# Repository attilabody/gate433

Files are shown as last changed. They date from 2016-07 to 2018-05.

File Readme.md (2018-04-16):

# Shared parking space access controller

## Features

Gate433 uses cheap, standard (and insecure) gate opener remotes operating on 433 MHz to control entry and exit of vehicles allowed to acces the parking area.

Each gate opener supposed to be assigned to one vehicle and has unique code. The main purpose of it is to make unfair usage of the parking as inconvinient as possible using commodity gate opener remotes.

Features list:

* 1024 possible remote codes
* Position of each vehicle (inside, outside, unknown) is remembered. Gate opening will be denied for unexpected movements (e.g vehicle which is already inside tries to enter again)
* Access time limits by direction can be set independently for any vehicle (e.g can enter Monday to Friday from 08:30 to 17:00, can leave Monday to Friday from 08:30 to 17:30)
* Vehicle database snd device configuration stored in EEPROM
* Log stored on SD card
* Database changes can be imported from SD card
* Exceptional days (e.g. National holydays) database on SD card
* Automatic DST handling
* Simple command line interpreter on serial for database manipulation, date/time setting, log manipulation and temperature query

## Hardware

There are two versions of the hardware: Original version used Arduino Nano as central component. It is obsoleted by the newer version based on a popular STM32F103C8T6 based minimal board widely known as BluePill. It's actually cheaper on eBay or Aliexpress than the total cost of the components it contains.

Both versions ar using two inputs (usually coming from inductive loop detectors) in addition to the RF signal to decide if a vehicke intends to enter or exit. A pair of tricolor traffic lights provide feedback for drivers.

Both versions have 6 opto-isolated open drain output for 12V LED traffic lights,one opto-isolated open collector output for gate opening and two opto-isolated input for inductive loop detectors.

Second iteration have three extra features compared to the first:

* WiFi to serial bridge for wireless communication
* Rotary encoder driven simpe user interface (yet to be implemented in the firmware)
* 3D printable case modelled in FreeCAD

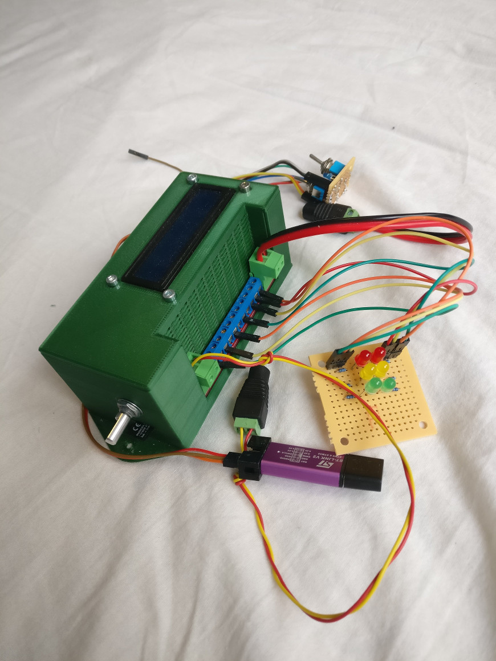
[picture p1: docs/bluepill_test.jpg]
V2


Prototype of STM32 based version

## Firmware

Arduino Nano based firware was built on Arduino framework using Sloeber Arduino IDE. Source files persist in folders named "gatekeeper", "common" and "libs".  
STM32 version is completely separated as it is based on STM32Cube framework. STM32 sources are placed in "gatekeeper-stm32" and "stm32goodies" folder.

## Schematics and PCB

Arduino based first version hardware developed using proprietrary Eagle free version, and obsoleted by STM32 version but schematics of the [mainboard](docs/V1_mainboard.pdf) and the [IO panel](docs/V1_extio.pdf) are still available for reference.

As mentioned above, hardware of STM32 version designed using KiCAD. The complete EDA project is available in the hardware/STM32 folder. Here are the [schematics](docs/bluepill.pdf) in PDF for easier access.

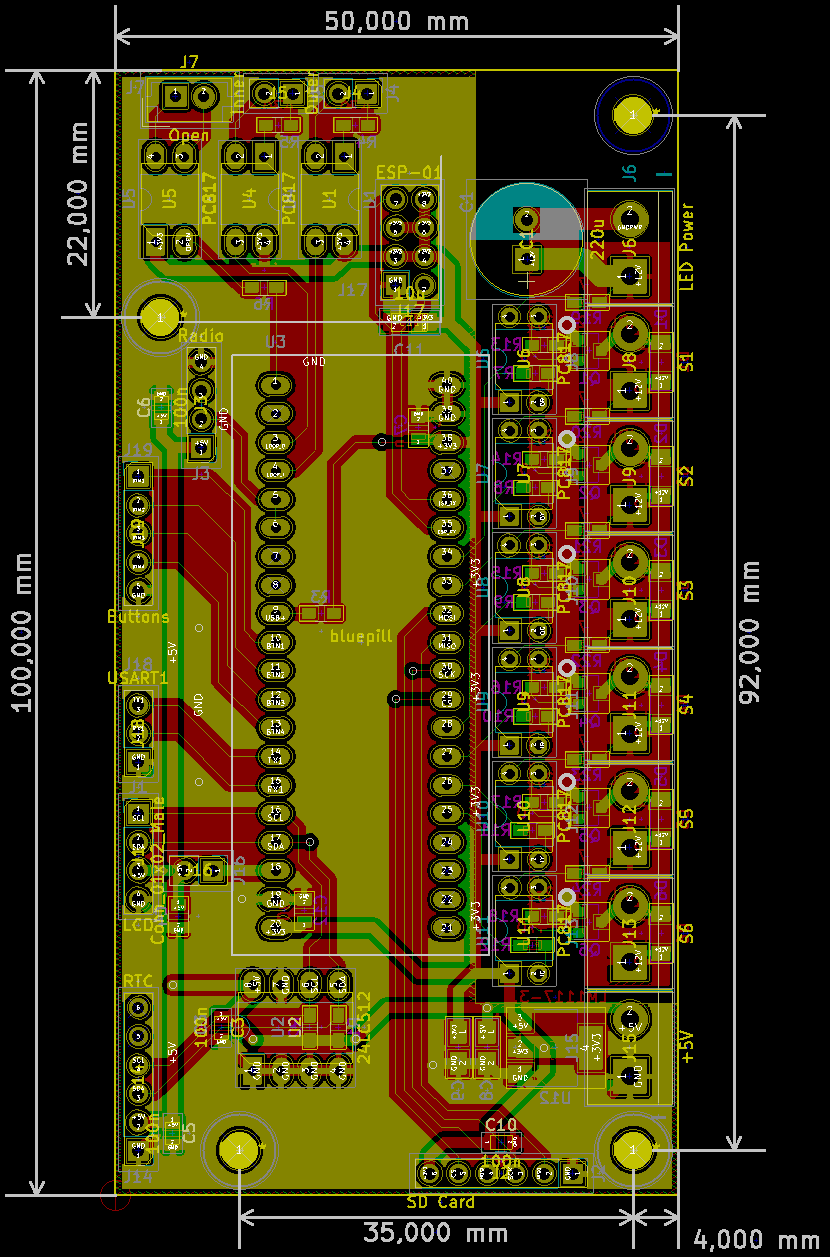
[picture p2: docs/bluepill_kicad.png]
bluepill_kicad


PCB design for STM32 bsed version

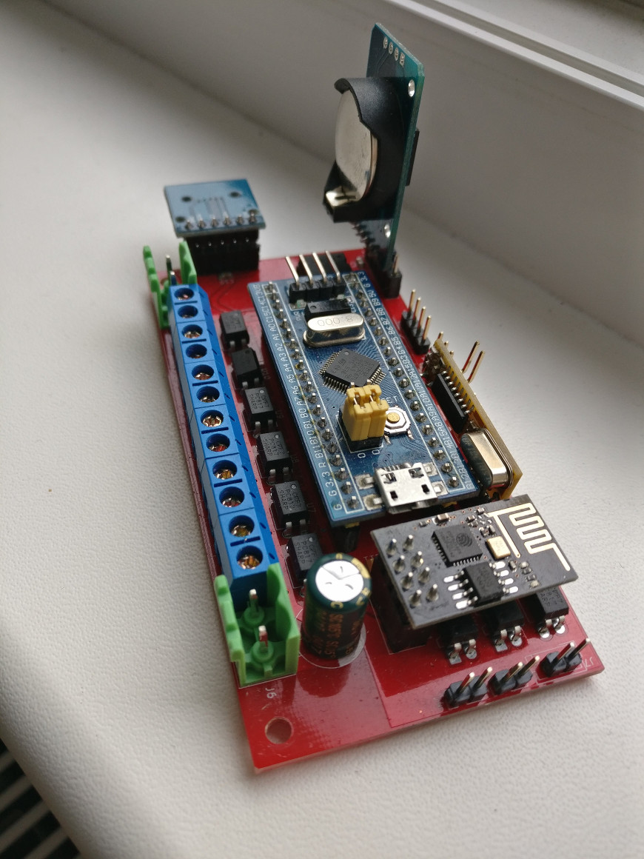
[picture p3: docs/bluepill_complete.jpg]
bluepill_complete


Assembled STM32 panel with modules installed

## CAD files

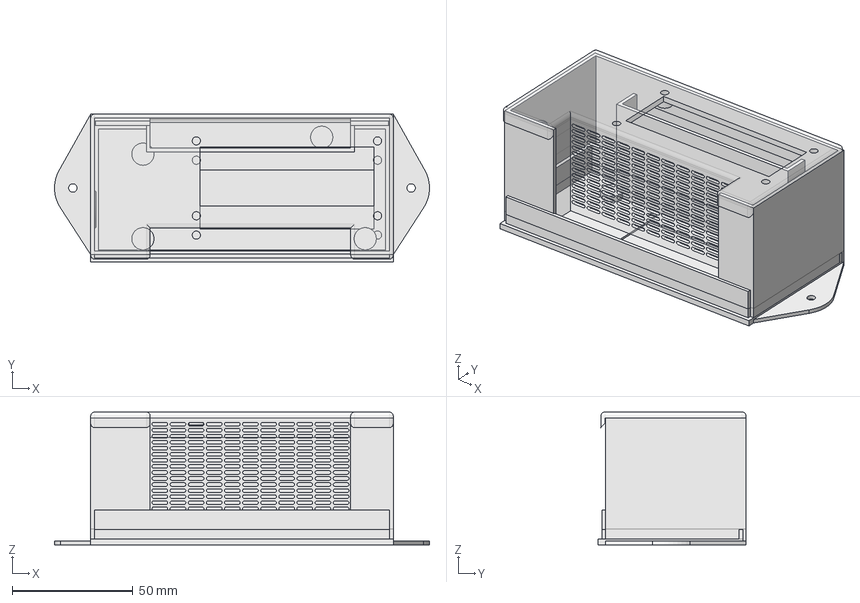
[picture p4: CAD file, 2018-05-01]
hardware/stm32/GateKeeperCase.fcstd
155.2 x 61.2 x 55.0 mm
EncoderHemChamf
Clone of Cap
Bottom
walls_low
walls_high
sdhole

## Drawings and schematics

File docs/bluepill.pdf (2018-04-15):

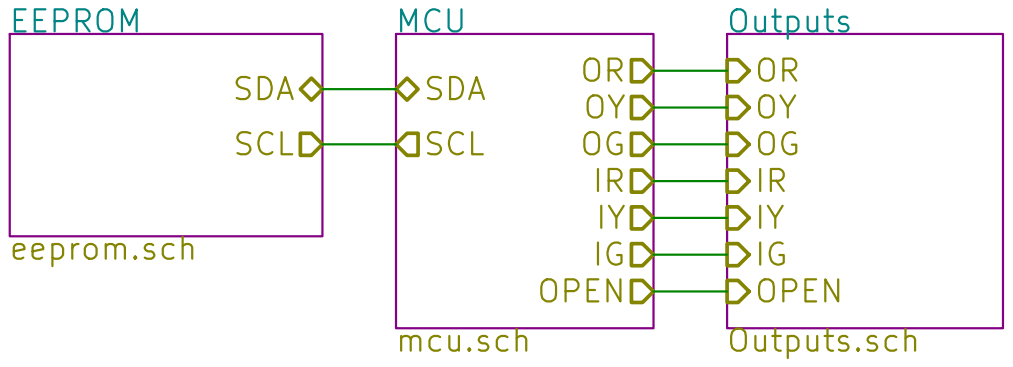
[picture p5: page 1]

File: bluepill.sch Sheet: / EEPROM

MCU mcu.sch SDA

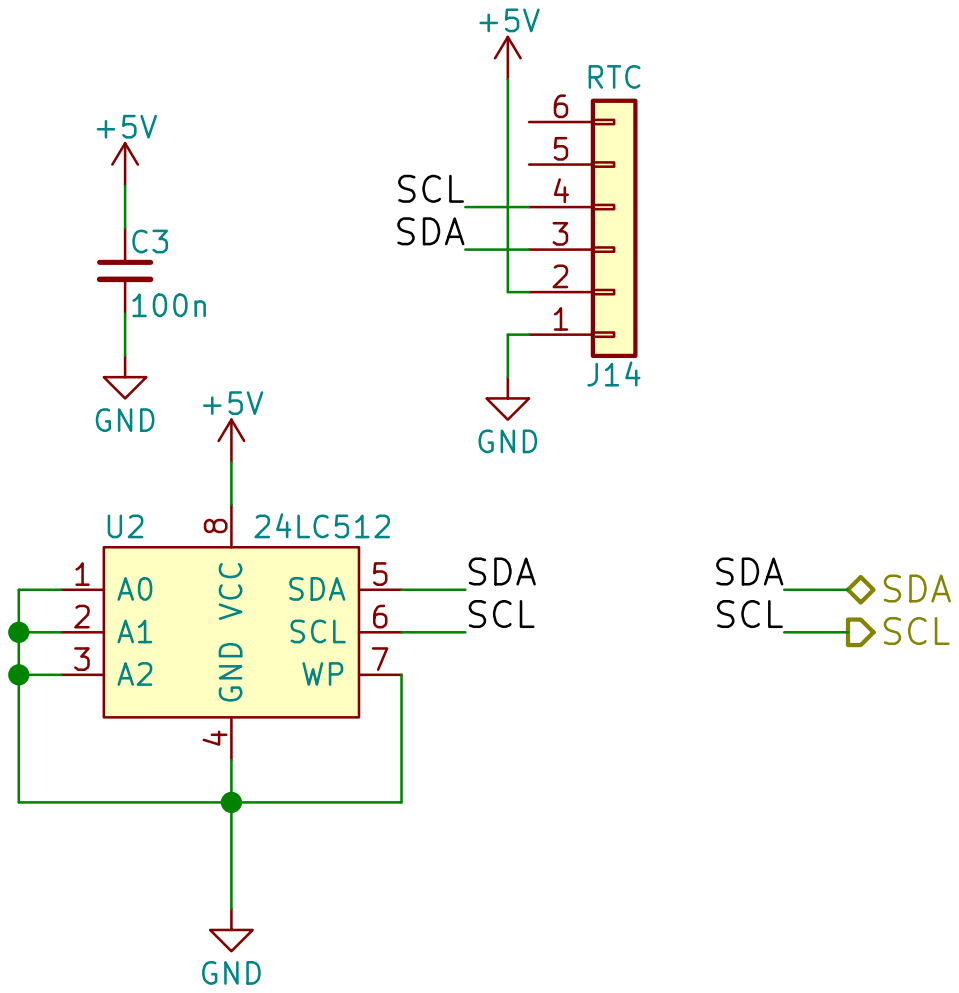
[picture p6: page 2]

8 A0 1 A1 2 A2 3 SDA 5 SCL 6 WP 7 U2 24LC512 SCL

File: eeprom.sch Sheet: /EEPROM/ GND

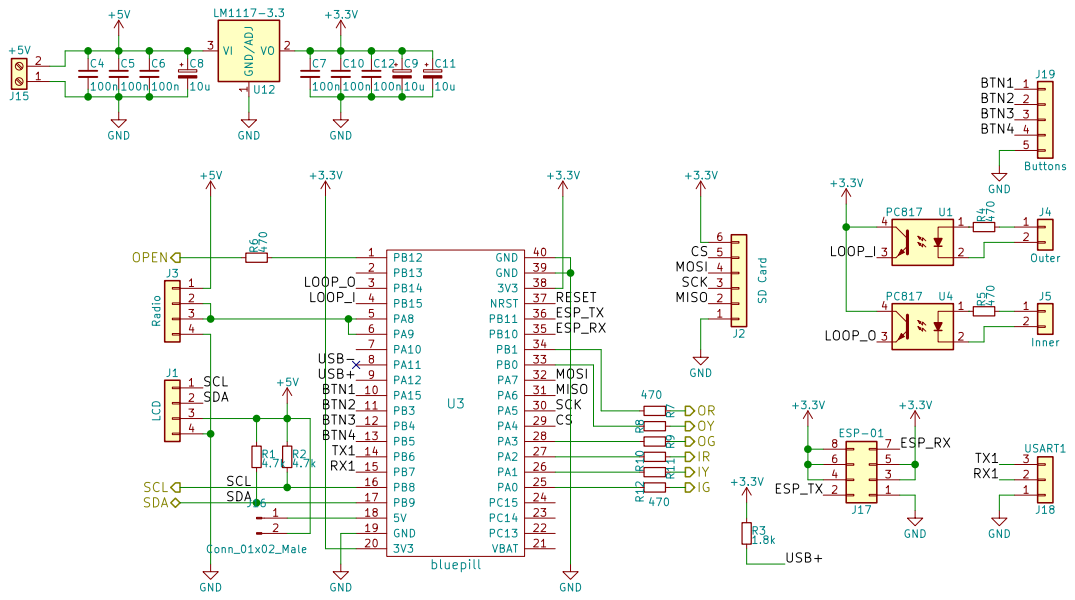
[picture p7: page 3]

SDA

Id: 3/4 Title: File: mcu.sch Sheet: /MCU/

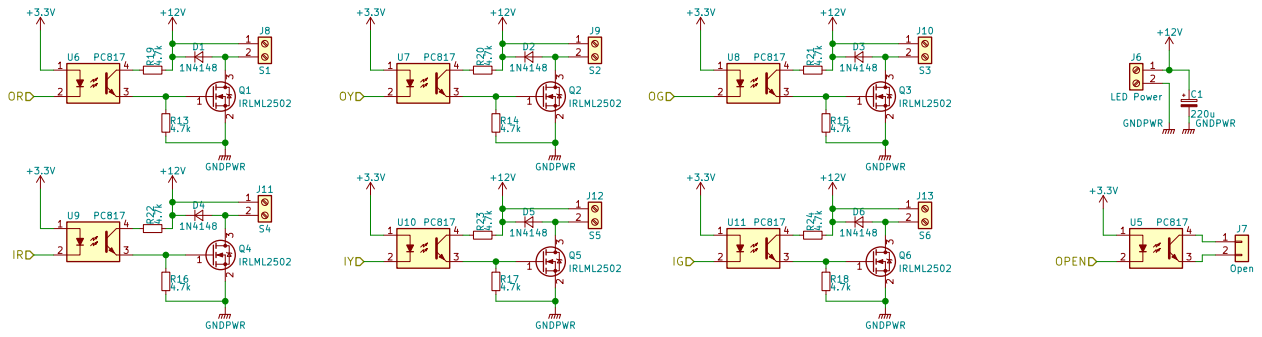
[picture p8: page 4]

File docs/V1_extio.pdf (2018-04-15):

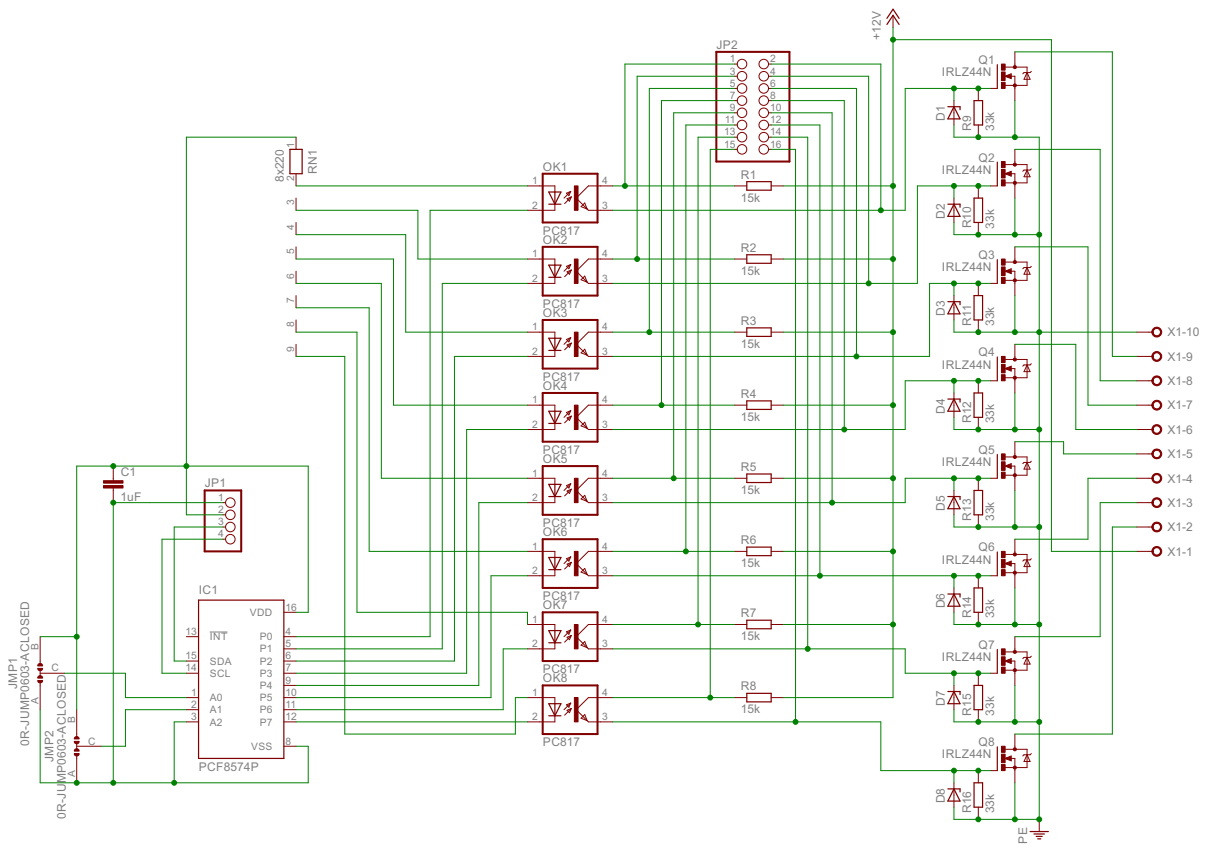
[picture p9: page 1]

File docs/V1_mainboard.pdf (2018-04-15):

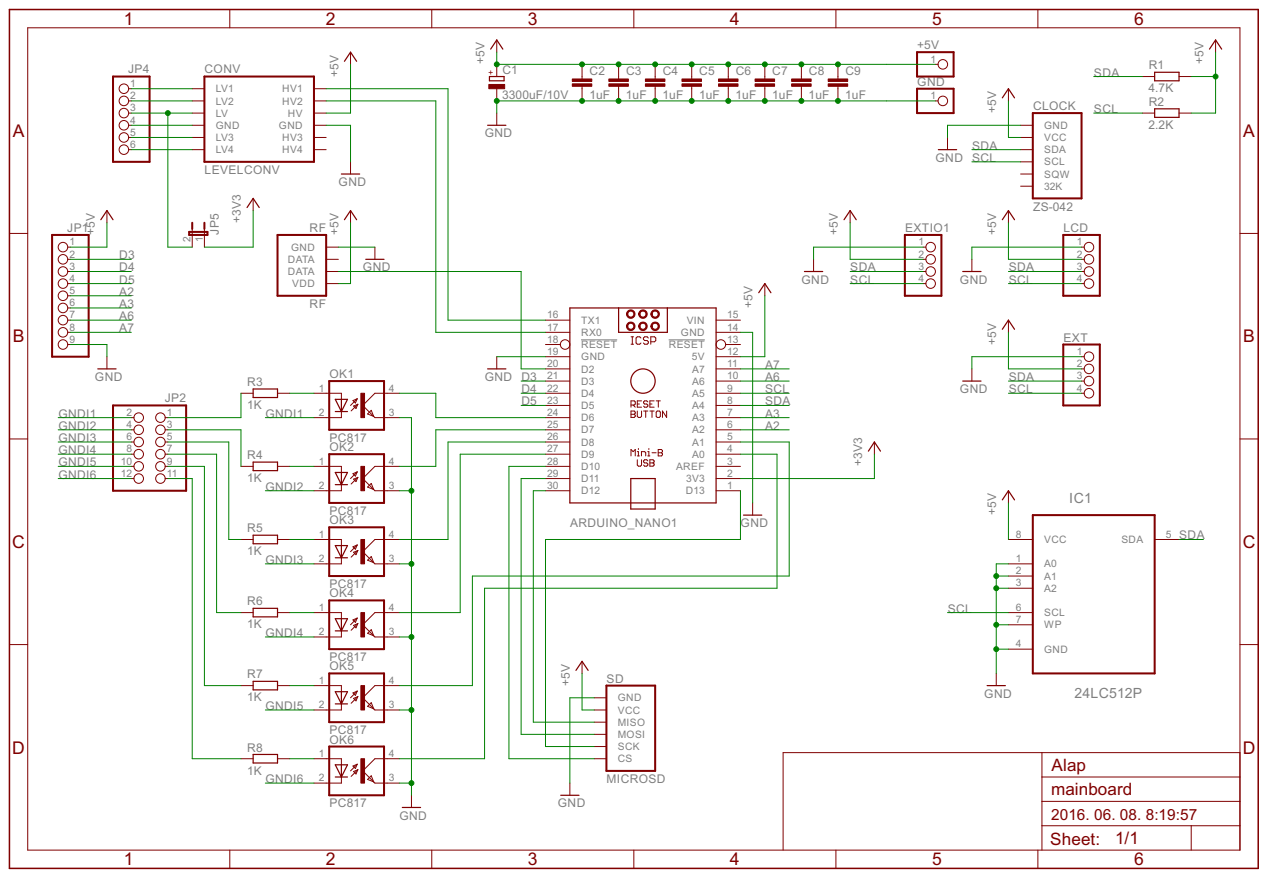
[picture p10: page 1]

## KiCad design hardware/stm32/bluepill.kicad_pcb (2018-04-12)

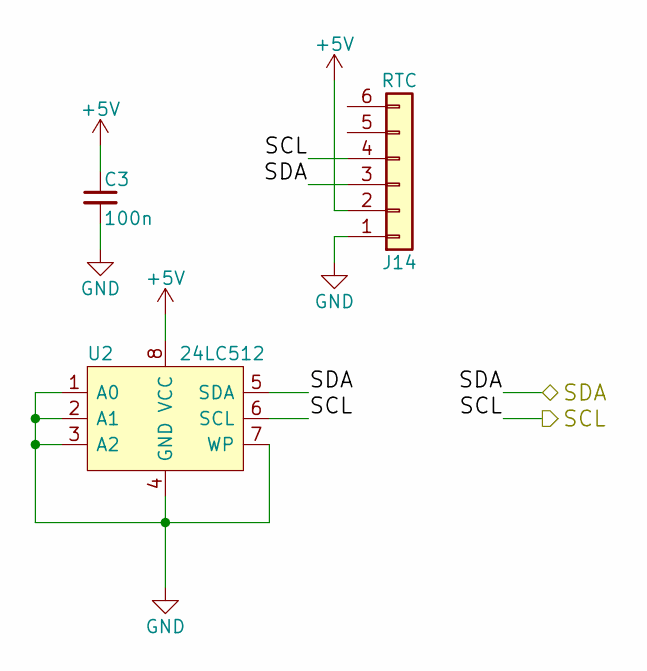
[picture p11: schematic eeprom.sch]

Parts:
C3: 100n; C_0805
J14: RTC; Pin_Header_Straight_1x06_Pitch2.54mm
U2: 24LC512; DIP-8_W7.62mm_LongPads

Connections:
+5V: C3.1, J14.2, U2.8 (VCC); also elsewhere on the board
/EEPROM/SCL: J14.4, U2.6 (SCL); also elsewhere on the board
/EEPROM/SDA: J14.3, U2.5 (SDA); also elsewhere on the board
GND: C3.2, J14.1, U2.1 (A0), U2.2 (A1), U2.3 (A2), U2.4 (GND), U2.7 (WP); also elsewhere on the board

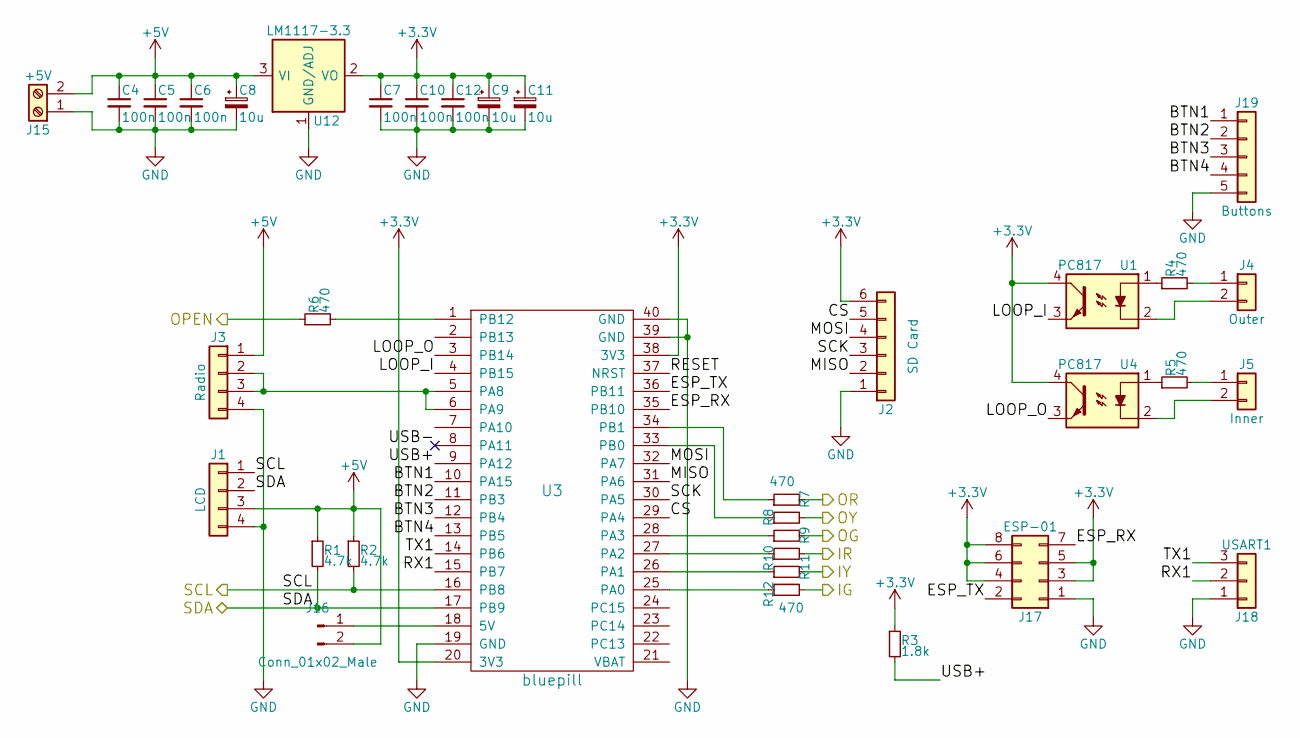
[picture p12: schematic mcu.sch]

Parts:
C4, C5, C6, C7, C10, C12: 100n; C_0805
C8, C9, C11: 10u; CP_Tantalum_Case-A_EIA-3216-18_Reflow
J1: LCD; Pin_Header_Straight_1x04_Pitch2.54mm
J2: SD Card; Pin_Header_Straight_1x06_Pitch2.54mm
J3: Radio; Pin_Header_Straight_1x04_Pitch2.54mm
J4: Outer; Pin_Header_Straight_1x02_Pitch2.54mm
J5: Inner; Pin_Header_Straight_1x02_Pitch2.54mm
J15: +5V; TerminalBlock_bornier-2_P5.08mm
J16: Conn_01x02_Male; Pin_Header_Straight_1x02_Pitch2.54mm
J17: ESP-01; Socket_Strip_Straight_2x04_Pitch2.54mm
J18: USART1; Pin_Header_Straight_1x03_Pitch2.54mm
J19: Buttons; Pin_Header_Straight_1x05_Pitch2.54mm
R1, R2: 4.7k; R_0603_HandSoldering
R3: 1.8k; R_0603_HandSoldering
R4, R5, R6, R7, R8, R9, R10, R11, R12: 470; R_0603_HandSoldering
U1, U4: PC817; DIP-4_W7.62mm_LongPads
U3: bluepill
U12: LM1117-3.3; SOT-223

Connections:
+3V3: C7.1, C9.1, C10.1, C11.1, C12.1, J2.6, J17.3, J17.4, J17.5, J17.6, J17.8, R3.1, U1.4, U3.20 (3V3), U3.38 (3V3), U4.4, U12.2 (VO), U12.4 (VO); also elsewhere on the board
+5V: C4.1, C5.1, C6.1, C8.1, J1.3, J3.1, J15.2, J16.2, R1.1, R2.1, U12.3 (VI); also elsewhere on the board
/EEPROM/SCL: J1.1, R2.2, U3.16 (PB8); also elsewhere on the board
/EEPROM/SDA: J1.2, R1.2, U3.17 (PB9); also elsewhere on the board
/MCU/BTN1: J19.1, U3.10 (PA15)
/MCU/BTN2: J19.2, U3.11 (PB3)
/MCU/BTN3: J19.3, U3.12 (PB4)
/MCU/BTN4: J19.4, U3.13 (PB5)
/MCU/CS: J2.5, U3.29 (PA4)
/MCU/ESP_RX: J17.7, U3.35 (PB10)
/MCU/ESP_TX: J17.2, U3.36 (PB11)
/MCU/IG: R12.2; also elsewhere on the board
/MCU/IR: R10.2; also elsewhere on the board
/MCU/IY: R11.2; also elsewhere on the board
/MCU/LOOP_I: U1.3, U3.4 (PB15)
/MCU/LOOP_O: U3.3 (PB14), U4.3
/MCU/MISO: J2.2, U3.31 (PA6)
/MCU/MOSI: J2.4, U3.32 (PA7)
/MCU/OG: R9.2; also elsewhere on the board
/MCU/OPEN: R6.1; also elsewhere on the board
/MCU/OR: R7.2; also elsewhere on the board
/MCU/OY: R8.2; also elsewhere on the board
/MCU/RX1: J18.2, U3.15 (PB7)
/MCU/SCK: J2.3, U3.30 (PA5)
/MCU/TX1: J18.3, U3.14 (PB6)
/MCU/USB+: R3.2, U3.9 (PA12)
GND: C4.2, C5.2, C6.2, C7.2, C8.2, C9.2, C10.2, C11.2, C12.2, J1.4, J2.1, J3.4, J15.1, J17.1, J18.1, J19.5, U3.19 (GND), U3.39 (GND), U3.40 (GND), U12.1 (GND/ADJ); also elsewhere on the board
unnamed: J3.2, J3.3, U3.5 (PA8), U3.6 (PA9)
unnamed: J4.1, R4.2
unnamed: J4.2, U1.2
unnamed: J5.1, R5.2
unnamed: J5.2, U4.2
unnamed: J16.1, U3.18 (5V)
unnamed: R4.1, U1.1
unnamed: R5.1, U4.1
unnamed: R6.2, U3.1 (PB12)
unnamed: R7.1, U3.34 (PB1)
unnamed: R8.1, U3.33 (PB0)
unnamed: R9.1, U3.28 (PA3)
unnamed: R10.1, U3.27 (PA2)
unnamed: R11.1, U3.26 (PA1)
unnamed: R12.1, U3.25 (PA0)

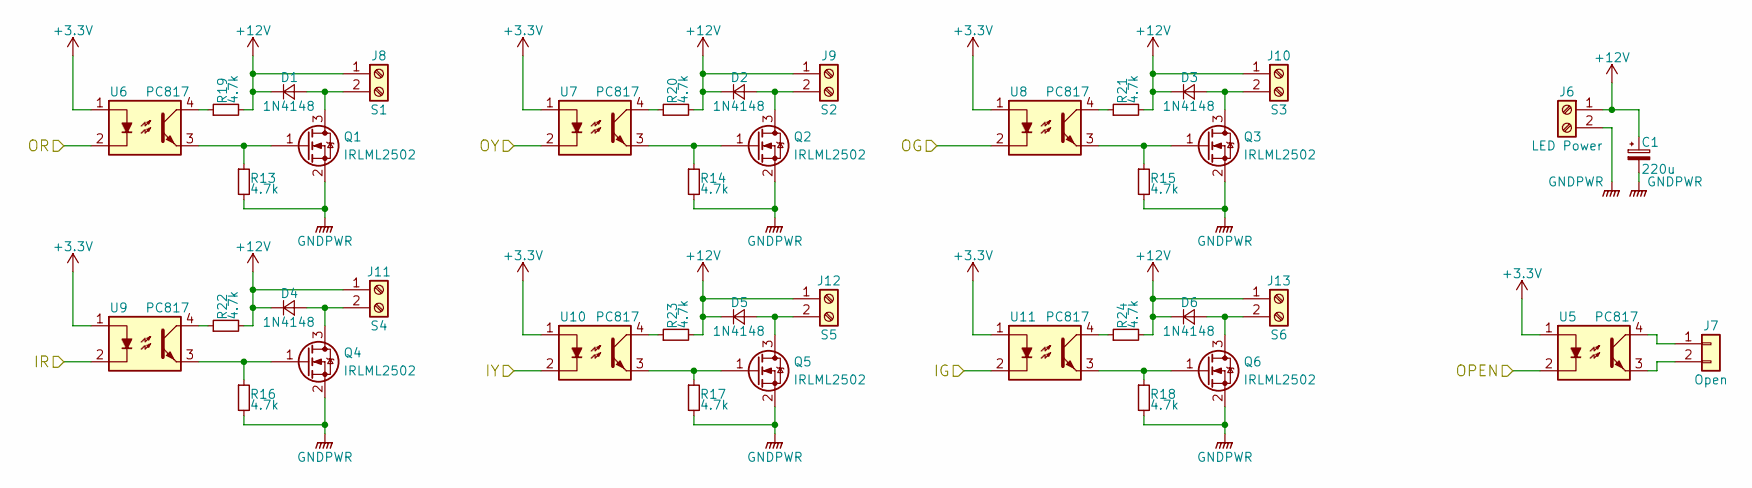
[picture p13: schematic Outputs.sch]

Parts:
C1: 220u; CP_Radial_D10.0mm_P3.50mm
D1, D2, D3, D4, D5, D6: 1N4148; D_MiniMELF
J6: LED Power; TerminalBlock_bornier-2_P5.08mm
J7: Open; JST_EH_B02B-EH-A_02x2.50mm_Straight
J8: S1; TerminalBlock_bornier-2_P5.08mm
J9: S2; TerminalBlock_bornier-2_P5.08mm
J10: S3; TerminalBlock_bornier-2_P5.08mm
J11: S4; TerminalBlock_bornier-2_P5.08mm
J12: S5; TerminalBlock_bornier-2_P5.08mm
J13: S6; TerminalBlock_bornier-2_P5.08mm
Q1, Q2, Q3, Q4, Q5, Q6: IRLML2502; SOT-23
R13, R14, R15, R16, R17, R18, R19, R20, R21, R22, R23, R24: 4.7k; R_0603_HandSoldering
U5: PC817; DIP-4_W7.62mm_LongPads
U6, U7, U8, U9, U10, U11: PC817; DIP-4_W7.62mm

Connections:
+3V3: U5.1, U6.1, U7.1, U8.1, U9.1, U10.1, U11.1; also elsewhere on the board
+12V: C1.1, D1.1 (K), D2.1 (K), D3.1 (K), D4.1 (K), D5.1 (K), D6.1 (K), J6.1, J8.1, J9.1, J10.1, J11.1, J12.1, J13.1, R19.2, R20.2, R21.2, R22.2, R23.2, R24.2
/MCU/IG: U11.2; also elsewhere on the board
/MCU/IR: U9.2; also elsewhere on the board
/MCU/IY: U10.2; also elsewhere on the board
/MCU/OG: U8.2; also elsewhere on the board
/MCU/OPEN: U5.2; also elsewhere on the board
/MCU/OR: U6.2; also elsewhere on the board
/MCU/OY: U7.2; also elsewhere on the board
GNDPWR: C1.2, J6.2, Q1.2 (S), Q2.2 (S), Q3.2 (S), Q4.2 (S), Q5.2 (S), Q6.2 (S), R13.2, R14.2, R15.2, R16.2, R17.2, R18.2
unnamed: D1.2 (A), J8.2, Q1.3 (D)
unnamed: D2.2 (A), J9.2, Q2.3 (D)
unnamed: D3.2 (A), J10.2, Q3.3 (D)
unnamed: D4.2 (A), J11.2, Q4.3 (D)
unnamed: D5.2 (A), J12.2, Q5.3 (D)
unnamed: D6.2 (A), J13.2, Q6.3 (D)
unnamed: J7.1, U5.4
unnamed: J7.2, U5.3
unnamed: Q1.1 (G), R13.1, U6.3
unnamed: Q2.1 (G), R14.1, U7.3
unnamed: Q3.1 (G), R15.1, U8.3
unnamed: Q4.1 (G), R16.1, U9.3
unnamed: Q5.1 (G), R17.1, U10.3
unnamed: Q6.1 (G), R18.1, U11.3
unnamed: R19.1, U6.4
unnamed: R20.1, U7.4
unnamed: R21.1, U8.4
unnamed: R22.1, U9.4
unnamed: R23.1, U10.4
unnamed: R24.1, U11.4

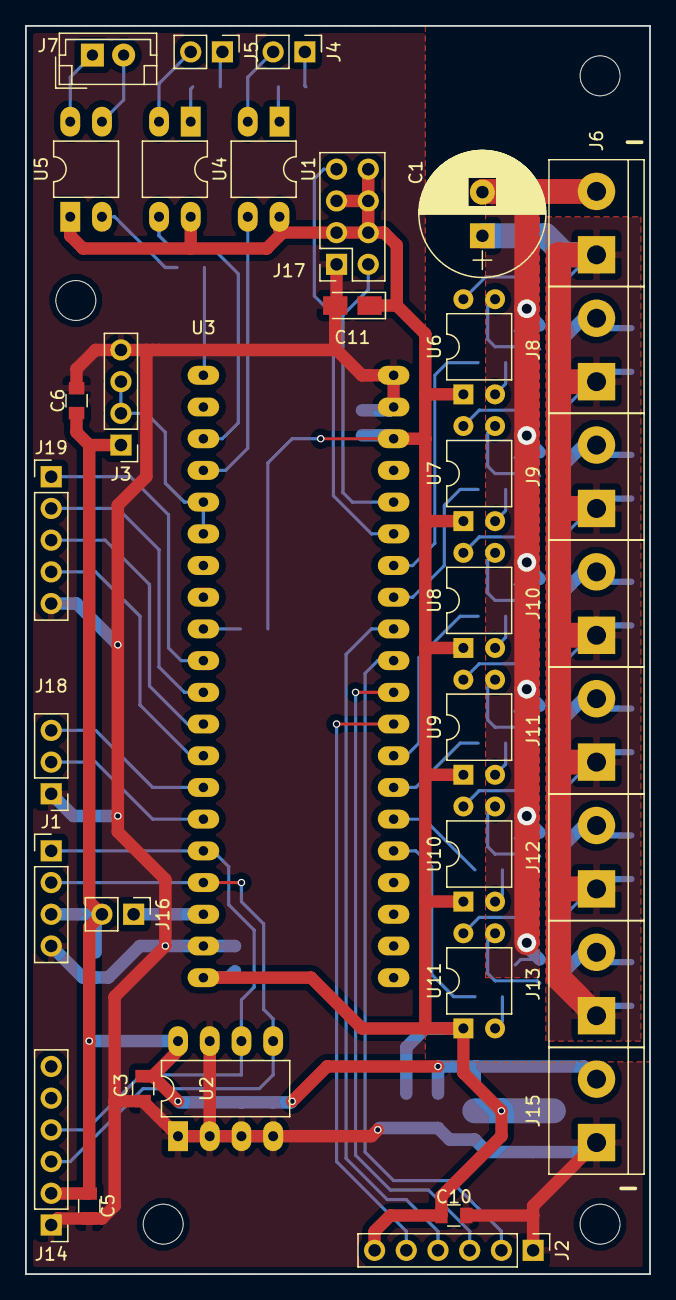
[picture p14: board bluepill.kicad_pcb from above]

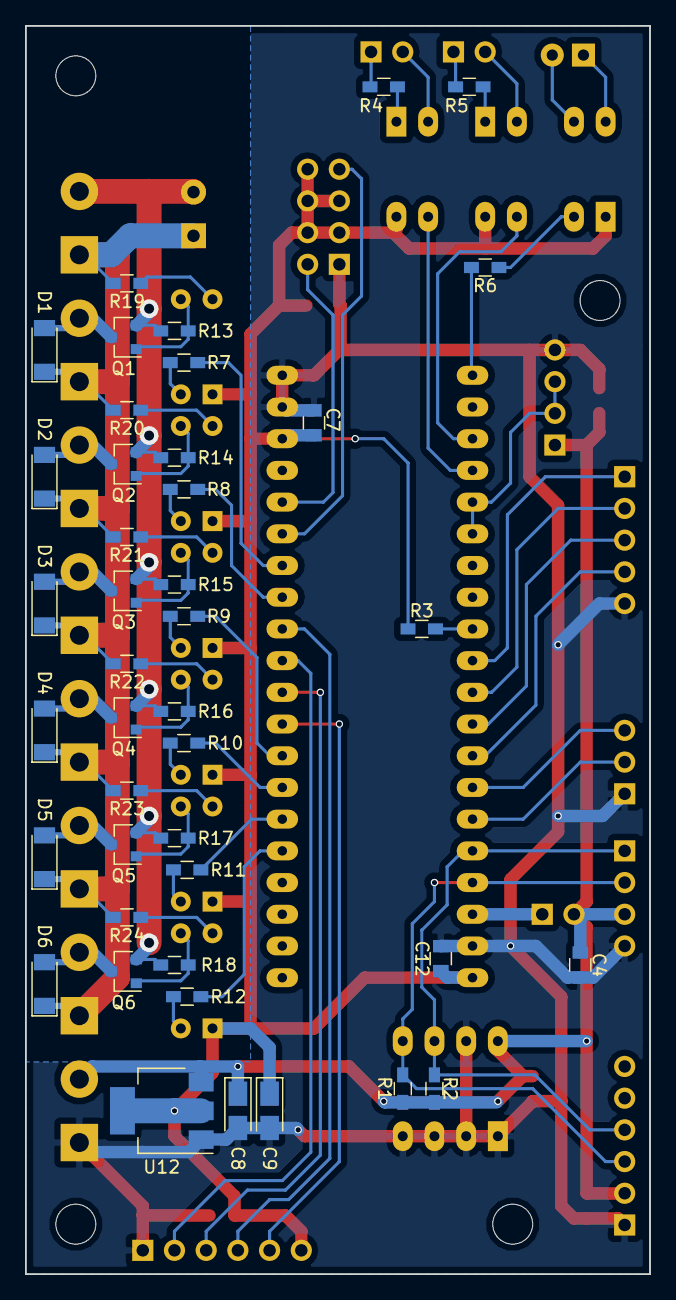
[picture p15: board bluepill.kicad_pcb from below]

Board: 2 copper layers, 50.0 x 100.0 mm, 78 parts (42 on the bottom side), 64 nets.

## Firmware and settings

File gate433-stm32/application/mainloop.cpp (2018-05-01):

/*
 * mainloop.cpp
 *
 *  Created on: Jan 11, 2018
 *      Author: compi
 */
#include <ctype.h>
#include <rfdecoder.h>
#include "stm32f1xx_hal.h"
#include "main.h"
#include "i2c.h"
#include "spi.h"
#include "usart.h"
#include "gpio.h"

#include <sg/ItLock.h>


#include "config.h"

#include "mainloop.h"

//#define TESTLOOP
//#define TEST_SDCARD
#define TEST_EEPROM
#define TEST_RTC

#if defined(TEST_SDCARD)
#include "SdFile.h"
#endif	//	TEST_SDCARD


extern "C" void _MainLoop();
extern "C" void HAL_SYSTICK_Callback(void);
extern "C" void HAL_GPIO_EXTI_Callback(uint16_t GPIO_Pin);


bool g_mainLoppReady = false;

char g_stateSigns[States::NUMSTATES] = { ' ', 'W', 'C', 'A', 'W', 'D', 'U', 'H', 'P' };

////////////////////////////////////////////////////////////////////
void HAL_GPIO_EXTI_Callback(uint16_t GPIO_Pin)
{
	if(g_mainLoppReady)
		MainLoop::Instance().HAL_GPIO_EXTI_Callback(GPIO_Pin);
}

////////////////////////////////////////////////////////////////////
void _MainLoop()
{
	Config::Instance().Load();

	MainLoop::Instance().Loop();
}

////////////////////////////////////////////////////////////////////
void HAL_SYSTICK_Callback(void)
{
	uint32_t	now = HAL_GetTick();
	if(g_mainLoppReady)
		MainLoop::Instance().Tick(now);
}

////////////////////////////////////////////////////////////////////
MainLoop::MainLoop()
: RotaryDecoder(this, 2, BTN_CLK_GPIO_Port, BTN_CLK_Pin, BTN_DATA_GPIO_Port, BTN_DATA_Pin, BTN_SW_GPIO_Port, BTN_SW_Pin)
, m_lights(256, 128)
, m_gate(OPEN_GPIO_Port, OPEN_Pin, false)
, m_com(&huart1, sg::UsartCallbackDispatcher::Instance(), m_serialOutRingBuffer, sizeof(m_serialOutRingBuffer), true)
, m_wifi(&huart3, sg::UsartCallbackDispatcher::Instance(), m_wifiOutRingBuffer, sizeof(m_wifiOutRingBuffer), true)
, m_i2c(I2c1::Instance())
, m_db(MainI2cEeprom::Instance(), (sizeof(ConfigData)/I2CEEPROMPAGELENGTH+1)*I2CEEPROMPAGELENGTH)
, m_rtc(m_i2c)
, m_lcd(m_i2c, Config::Instance().lcdI2cAddress)
, m_decoder(RFDecoder::Instance())
, m_loop(LOOP_I_GPIO_Port, LOOP_I_Pin, LOOP_O_GPIO_Port, LOOP_O_Pin, true)
, m_log("LOG.TXT")
, m_proc(*this)
{
	m_decoder.Init(*this);
}

////////////////////////////////////////////////////////////////////
#define TICK(x) HAL_GPIO_TogglePin(GPIOC, GPIO_PIN_13); m_com << x << "\r\n"
#define MSG(x)	m_com << x << "\r\n";

////////////////////////////////////////////////////////////////////
void MainLoop::Fail(const char * file, int line)
{
	m_com << file << ": " << (uint32_t)line << "\r\n";
	m_wifi << file << ": " << (uint32_t)line << "\r\n";
	while(1) {
		HAL_GPIO_TogglePin(GPIOC, GPIO_PIN_13);
		HAL_Delay(100);
	}
}

#define FAIL() Fail(__FILE__, __LINE__)

//////////////////////////////////////////////////////////////////////
//void MainLoop::DumpBufferLine(uint8_t *buffer, uint16_t base, uint16_t offset, uint8_t count)
//{
//	m_com << sg::Usart::hex << sg::Usart::pad << (uint16_t)(base + offset);
//	while(count--) {
//		m_com << ' ' << buffer[offset++];
//	}
//	m_com << sg::Usart::endl;
//
//}

////////////////////////////////////////////////////////////////////
void MainLoop::LineReceived(char *buffer, uint16_t count)
{
	HAL_StatusTypeDef ret;
	(void)ret;

	if(buffer != m_serialBuffer && buffer != m_wifiBuffer)
		return;
	if(buffer == m_serialBuffer && m_serialLineReceived) {
		ret = m_com.Receive(m_serialBuffer, sizeof(m_serialBuffer), *this);
		return;
	} else if( buffer == m_wifiBuffer && m_wifiLineReceived) {
		ret = m_wifi.Receive(m_wifiBuffer, sizeof(m_wifiBuffer), *this);
		return;
	}

	char *bufPtr = buffer + count -1;
	while(bufPtr >= buffer && (*bufPtr == '\r' || *bufPtr == '\n' || !*bufPtr))
		--bufPtr;
	if(bufPtr < buffer + LINEBUFFER_SIZE - 1)
		*(bufPtr + 1) = 0;
	else
		buffer[ LINEBUFFER_SIZE - 1] = 0;

	if(buffer == m_serialBuffer)
		m_serialLineReceived = true;
	else
		m_wifiLineReceived = true;
}


////////////////////////////////////////////////////////////////////
// Called from ISR
////////////////////////////////////////////////////////////////////
void MainLoop::CodeReceived(uint16_t code)
{
	if(!m_codeReceived) {
		m_code = code;
		m_codeReceived = true;
	}
	uint32_t now = HAL_GetTick();
	if(m_codeLogQueueIndex < CODE_LOG_QUEUE_SIZE && (m_lastCodeReceived != code || now - m_lastCodeReceivedTick > 1000))
		m_codeLogQueue[m_codeLogQueueIndex++] = code;

	m_lastCodeReceived = code;
	m_lastCodeReceivedTick = now;
}

////////////////////////////////////////////////////////////////////
// Called from ISR
////////////////////////////////////////////////////////////////////
void MainLoop::Step(bool up)
{
	if(up) m_rotaryCounter++;
	else m_rotaryCounter--;
}

////////////////////////////////////////////////////////////////////
// Called from ISR
////////////////////////////////////////////////////////////////////
void MainLoop::Click(bool on)
{
	m_rotaryButton = on;
}


////////////////////////////////////////////////////////////////////
void MainLoop::Tick(uint32_t now)
{
	m_lights.Tick(now);
	m_loop.Tick(now);
	m_gate.Tick(now);
}

////////////////////////////////////////////////////////////////////
#ifdef TESTLOOP
void MainLoop::Loop()
{
	HAL_StatusTypeDef	ret = HAL_OK;
	bool				firstCode = true;
	uint8_t				eepromBuffer[256];

	for(uint8_t cnt = 0; cnt < 16; ++cnt) {
	  uint32_t start = SysTick->VAL;
	  while(SysTick->VAL - start < 1000 );
	  TICK('.');
	}
	m_com << "\r\n";

#ifdef TEST_SDCARD
	uint32_t byteswritten, bytesread;                     /* File write/read counts */
	uint8_t wtext[] = "This is STM32 working with FatFs\r\n"; /* File write buffer */
	uint8_t rtext[100];                                   /* File read buffer */

	uint32_t fpos = 0;
	SdFile sdFileW;

	m_lcd.Print("SD card");

	TICK("openw1");
	if(sdFileW.Open("STM32.TXT", static_cast<SdFile::OpenMode>(SdFile::CREATE_ALWAYS | SdFile::WRITE))) {
		SdFile sdFileR;
		TICK("openr1");
		if(sdFileR.Open("FILE.TXT", static_cast<SdFile::OpenMode>(SdFile::OPEN_EXISTING | SdFile::READ))) {
			TICK("read1");
			if((bytesread = sdFileR.Read(rtext, sizeof(rtext))) != 0) {
				m_com << sg::Usart::Buffer(rtext, bytesread) << "\r\n";
				fpos = sdFileR.Ftell();
				TICK("write1.1");
				byteswritten = sdFileW.Write(wtext, sizeof(wtext)-1);
				TICK("closer1");
				sdFileR.Close();
				if(byteswritten) {
					TICK("closew1");
					sdFileW.Close();
					if(sdFileW.Open("STM32.TXT", static_cast<SdFile::OpenMode>(SdFile::OPEN_EXISTING | SdFile::WRITE))) {
						sdFileW.Seek(sdFileW.Size());
						TICK("write1.2");
						byteswritten = sdFileW.Write(rtext, bytesread);
						TICK("closew1");
						sdFileW.Close();
					}
					TICK("openr2");
					if(sdFileR.Open("STM32.TXT", static_cast<SdFile::OpenMode>(SdFile::OPEN_EXISTING | SdFile::READ))) {
						do {
							TICK("read2");
							if((bytesread = sdFileR.Read(rtext, sizeof(rtext))))
								m_com.Send(rtext, bytesread);
						} while(bytesread != 0);
						TICK("closer2");
						sdFileR.Close();
					} else FAIL();
				} else FAIL();
			} else FAIL();
		} else FAIL();
	} else FAIL();
	(void)fpos;
#endif	//	TEST_SDCARD

	m_lcd.Clear();
	m_lcd.Print("EEPROM");

#ifdef TEST_EEPROM
	for(uint16_t i=0; i < sizeof(eepromBuffer); ++i)
		eepromBuffer[i] = 0xff-i;

	ret = m_i2cEeprom.Write(eepromBuffer, sizeof(eepromBuffer), sizeof(eepromBuffer));
	memset(eepromBuffer, 0xaa, sizeof(eepromBuffer));
	ret = m_i2cEeprom.Read(eepromBuffer, 0, sizeof(eepromBuffer));
	if(ret == HAL_OK)
	{
		m_i2cEeprom.Sync();
		for(uint16_t offset = 0; offset < sizeof(eepromBuffer); offset += 32)
			DumpBufferLine(eepromBuffer, 0, offset, 32);
		m_com << sg::Usart::endl;

		ret = m_i2cEeprom.Read(eepromBuffer, sizeof(eepromBuffer), sizeof(eepromBuffer));
		if(ret == HAL_OK) {
			m_i2cEeprom.Sync();
			for(uint16_t offset = 0; offset < sizeof(eepromBuffer); offset += 32)
				DumpBufferLine(eepromBuffer, sizeof(eepromBuffer), offset, 32);
			m_com << sg::Usart::endl;
		}
	}

	database::dbrecord	rec;
	m_db.getParams(0, rec);

	uint16_t	base = 0;
#endif	//	TEST_EEPROM

#ifdef TEST_RTC
	using Ts = sg::DS3231::Ts;
	ret = m_rtc.Init();
	Ts		ts;
	bool	desync = false;
#endif	//	TEST_RTC
	ret = m_com.Receive(m_serialOutRingBuffer, sizeof(m_serialOutRingBuffer), *this);

	uint32_t	counter = 0;
	while(true)
	{
		uint32_t offset = 0;
		for(uint8_t u = 0; u < m_lights.COUNT; ++u) {
			uint32_t curval = (counter+offset) & 0x1fff;
			m_lights.Set(u, curval > 4096 ? 8192 - curval : curval);
			offset += 4096/5;
		}
		counter += 256;

		auto firstTick = HAL_GetTick();
		do {
			if(m_serialLineReceived) {
				m_com << m_serialOutRingBuffer << "\r\n";
				m_serialLineReceived = false;
				ret = m_com.Receive(m_serialOutRingBuffer, sizeof(m_serialOutRingBuffer), *this);
			}
		} while(HAL_GetTick() - firstTick < 20 );

		if(counter >= 8192)
		{
			counter -= 8192;
#ifdef TEST_RTC
			ret = m_rtc.Get(ts, desync);
			m_com << sg::Usart::dec << (ts.hour < 10 ? "0" : "") << ts.hour << (ts.min < 10 ? ":0" : ":") << ts.min << (ts.sec < 10 ? ":0" : ":") << ts.sec << "  ";
#else
			TICK('#');
#endif
			if(m_codeReceived) {
				auto code = m_code;
				m_codeReceived = false;
				m_com << code;
				if(firstCode) {
					m_lcd.Clear();
					firstCode = false;
				} else
					m_lcd.SetCursor(0, 0);
				m_lcd.Print(code, false, 4);
			}
			m_com << sg::Usart::endl;

			HAL_GPIO_TogglePin(GPIOC, GPIO_PIN_13);
#if defined(TEST_EEPROM)
			m_com << sg::Usart::endl;
			ret = m_i2cEeprom.Read(eepromBuffer, base, sizeof(eepromBuffer));
			m_i2cEeprom.Sync();
			for(uint16_t offset = 0; offset < sizeof(eepromBuffer); offset += 32)
				DumpBufferLine(eepromBuffer, base, offset, 32);
			m_com << sg::Usart::endl << sg::Usart::endl;
			base += 256;
#endif
		}
	}
	(void)ret;
}
#else	//	TESTLOOP

////////////////////////////////////////////////////////////////////
void MainLoop::Loop()
{
	HAL_StatusTypeDef		ret = HAL_OK;
	uint32_t				oldTick, ellapsed;
	uint32_t				now, lastHeartbeat;
	sg::DS3231::Ts			ts;

	int32_t					counter = m_rotaryCounter;
	bool					button = m_rotaryButton;

	InductiveLoop::STATUS	ilStatus = InductiveLoop::NONE;
	bool					ilConflict = false;
	bool					inner = false;
	bool					ilChanged = false;
	
	g_mainLoppReady = true;

	{
		m_rtc.Get(m_rtcDateTime, m_rtcDesync);
		do {
			m_rtc.Get(ts, m_rtcDesync);
		} while(ts.sec == m_rtcDateTime.sec);
		m_rtcTick = HAL_GetTick();
		UpdateDow(ts);
		m_rtcDateTime = ts;
	}
	oldTick = m_rtcTick;
	lastHeartbeat = m_rtcTick;

	if((ret = m_com.Receive(m_serialBuffer, sizeof(m_serialBuffer), *this)) != HAL_OK)
		m_log.log(logwriter::ERROR, m_rtcDateTime, "m_com.Receive", ret);
	if((ret = m_wifi.Receive(m_wifiBuffer, sizeof(m_wifiBuffer), *this)) != HAL_OK)
		m_log.log(logwriter::ERROR, m_rtcDateTime, "m_wifi.Receive", ret);

	m_com << "\r\n" CMNTS  "READY\r\n";
	m_wifi << "\r\n" CMNTS "READY\r\n";

	while(true)
	{
		now = HAL_GetTick();

		if(m_com.GetAndClearError()) {
			if((ret = m_com.Receive(m_serialBuffer, sizeof(m_serialBuffer), *this)) != HAL_OK)
				m_log.log(logwriter::ERROR, m_rtcDateTime, "m_com.Receive", ret);
			m_serialLineReceived = false;
		}
		if(m_serialLineReceived) {
			if(m_serialBuffer[0])
				m_proc.Process(m_com, m_serialBuffer);
			m_serialLineReceived = false;
			ret = m_com.Receive(m_serialBuffer, sizeof(m_serialBuffer), *this);
		}
		if(m_wifi.GetAndClearError()) {
			if((ret = m_wifi.Receive(m_wifiBuffer, sizeof(m_wifiBuffer), *this)) != HAL_OK)
				m_log.log(logwriter::ERROR, m_rtcDateTime, "m_wifi.Receive", ret);
			m_wifiLineReceived = false;
		}
		if(m_wifiLineReceived) {
			if(m_wifiBuffer[0])
				m_proc.Process(m_wifi, m_wifiBuffer);
			m_wifiLineReceived = false;
			ret = m_wifi.Receive(m_wifiBuffer, sizeof(m_wifiBuffer), *this);
		}

		if(m_codeLogQueueIndex) {
			uint16_t code;
			{
				sg::ItLock	lock;
				code = m_codeLogQueue[--m_codeLogQueueIndex];
			}
			m_log.log(m_log.INFO, m_rtcDateTime, "RCV", code & 0x3ff, code >> 10, -1, -1, -1);

			if(code != m_lcd.GetLastReceivedId())
				m_lcd.UpdateLastReceivedId(code);
		}

		if(now != oldTick)
		{
			{
				sg::ItLock	lock;
				ilStatus = m_loop.GetStatus();
				ilConflict = m_loop.GetConflict();
			}
			ilChanged = ilStatus != m_ilStatus || ilConflict != m_ilConflict;

			if(ilChanged) {
				m_ilStatus = ilStatus;
				m_ilConflict = ilConflict;
				m_lcd.UpdateLoopStatus(ilStatus == InductiveLoop::INNER, ilStatus == InductiveLoop::OUTER, ilConflict);
				inner = ilStatus == InductiveLoop::INNER;
			}

			if(CheckDateTime(now))
				m_lcd.UpdateDt(m_rtcDateTime, m_rtcDesync);

			if(now - lastHeartbeat >= 500) {
				HAL_GPIO_TogglePin(GPIOC, GPIO_PIN_13);
				lastHeartbeat = now;
			}

			if(counter != m_rotaryCounter) {
				m_wifi << m_rotaryCounter << m_wifi.endl;
				counter = m_rotaryCounter;
			}
			if(button != m_rotaryButton) {
				m_wifi << (m_rotaryButton ? "ON" : "OFF") << m_wifi.endl;
				button = m_rotaryButton;
			}

			oldTick = now;
		}

		switch(m_state)
		{
		case States::OFF:
		case States::CONFLICT:
		case States::CODEWAIT:
			if(ilChanged)
			{
				ChangeState(ilStatus == InductiveLoop::NONE ? States::OFF : (ilConflict ? States::CONFLICT : States::CODEWAIT), inner, now);
			}
			else if(m_state == States::CODEWAIT && m_codeReceived)
			{
				if(m_code == m_countedCode) {	// received second time
					ChangeState(Authorize(m_code, inner), inner, now);
				} else {
					m_countedCode = m_code;
					m_codeReceived = false;
				}
			}

			break;

		case States::ACCEPT:
		case States::WARN:
		case States::HURRY:
		case States::PASSING:
			if(ilChanged) {
				if(ilStatus == InductiveLoop::NONE) {
					m_db.setStatus(m_countedCode, m_cycleInner ? database::dbrecord::OUTSIDE : database::dbrecord::INSIDE);
					ChangeState(States::OFF, inner, now);
				} else if(m_state != States::PASSING) {
					ChangeState(States::PASSING, inner, m_stateStartedTick);
				}
			} else if(m_state == States::ACCEPT || m_state == States::WARN) {
				ellapsed = now - m_stateStartedTick;
				if(ellapsed > Config::Instance().passTimeout * 1000)
					ChangeState(States::HURRY, inner, now);
			} else {
				ellapsed = now - m_stateStartedTick;
				if(ellapsed > Config::Instance().hurryTimeout * 1000)
					ChangeState(States::OFF, inner, now);
			}
			break;

		case States::DENY:
		case States::UNREGISTERED:
			if(ilChanged && ilStatus != (m_cycleInner ? InductiveLoop::INNER : InductiveLoop::OUTER)) {
				ChangeState(ilStatus == InductiveLoop::NONE ? States::OFF : (ilConflict ? States::CONFLICT : States::CODEWAIT), inner, now);
			}
			break;

		case States::NUMSTATES:	// should not happen
			break;
		}	//	switch(m_state)

		m_log.LogFromQueue(1);

	}	//	while(true)

	(void)ret;
}

////////////////////////////////////////////////////////////////////
void MainLoop::ChangeState(States newStatus, bool inner, uint32_t now)
{
	if(newStatus == States::CODEWAIT) {
		m_countedCode = -1;
		m_codeReceived = false;
		m_cycleInner = inner;
	} else if(newStatus == States::ACCEPT || newStatus == States::WARN) {
		m_gate.Set(500, 1500, now);
	} else if(newStatus == States::OFF)
		m_gate.Reset();

	m_stateStartedTick = now;
	m_lights.SetMode(newStatus, inner);
	m_state = newStatus;
}

////////////////////////////////////////////////////////////////////
// may return ACCEPT WARN DENY UNREGISTERED
States MainLoop::Authorize( uint16_t id, bool inner )
{
	database::dbrecord	rec;
	States				ret(States::ACCEPT);
	char				reason = ' ';

	uint16_t	mod( m_rtcDateTime.min + m_rtcDateTime.hour * 60 );
	uint8_t		dow( 1<<(m_rtcDateTime.wday - 1));

	if( !m_db.getParams(id & 0x3ff, rec) )
		return ret;


	if(!rec.in_start && !rec.in_end)
		ret = States::UNREGISTERED;
	else if( rec.position == ( inner ? database::dbrecord::OUTSIDE : database::dbrecord::INSIDE ) ) {
		ret = Config::Instance().relaxedPos ? States::WARN : States::DENY;
		reason = 'P';
	} else if(!m_rtcDesync)
	{
		States	timeFail = Config::Instance().relaxedDateTime ? States::WARN : States::DENY;
		if( !( rec.days & dow )) {
			ret = timeFail;
			reason = 'D';
		} else {
			uint16_t	start( inner ? rec.out_start : rec.in_start );
			uint16_t	end( inner ? rec.out_end : rec.in_end );

			if(mod < start || mod > end) {
				ret = timeFail;
				reason = 'T';
			}
		}
	}
	m_log.log(logwriter::INFO, m_rtcDateTime, "Auth", id&0x3ff, id >> 10, rec.position, inner, ret, reason );
	if((rec.days & 0x80) && ret == States::DENY)
		ret = States::WARN;

	m_lcd.UpdateLastDecision(ret, id, reason);
	return ret;
}

////////////////////////////////////////////////////////////////////
bool MainLoop::CheckDateTime(uint32_t now)
{
	sg::DS3231::Ts	ts;
	bool desync;

	if(now - m_rtcTick > 980) {
		m_rtc.Get(ts, desync);
		if(m_rtcDateTime.sec != ts.sec) {
			if(m_rtcDateTime.mday != ts.mday)
				UpdateDow(ts);
			m_rtcTick = now;
			m_rtcDateTime = ts;
			m_rtcDesync = desync;
			return true;
		}
	}
	return false;
}

////////////////////////////////////////////////////////////////////
void MainLoop::UpdateDow(sg::DS3231::Ts &ts)
{
	SdFile		f;
	char		buffer[17];
	const char	*bufPtr;
	uint8_t		month, day, dow;

	uint8_t	used = 0;
	FRESULT	fr;
	unsigned int	read;

	if(f.Open("SHUFFLE.TXT", static_cast<SdFile::OpenMode>(SdFile::OPEN_EXISTING | SdFile::READ )) == FR_OK)
	{
		do {
			if((fr = f.Read(buffer + used, sizeof(buffer) - 1 - used, &read)) == FR_OK) {
				used += read;
				buffer[used] = 0;
				bufPtr = buffer;
				if( (month = sg::GetIntParam(bufPtr)) != 0xff &&
					(day = sg::GetIntParam(bufPtr)) != 0xff &&
					(dow = sg::GetIntParam(bufPtr) != 0xff) &&
					month == ts.mon && day == ts.mday)
				{
					ts.wday = dow;
					break;
				}
				memmove(buffer, bufPtr, used - (bufPtr - buffer));
				used -= bufPtr - buffer;
			}
		} while(fr == FR_OK && (used || read));
		f.Close();
	}
}

#endif	//	TESTLOOP

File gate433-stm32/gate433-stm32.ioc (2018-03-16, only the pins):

Mcu.UserName=STM32F103C8Tx
PA0-WKUP.Signal=S_TIM2_CH1_ETR
PA1.Signal=S_TIM2_CH2
PA13.Signal=SYS_JTMS-SWDIO
PA14.Signal=SYS_JTCK-SWCLK
PA15.GPIO_Label=BTN_CLK
PA15.Signal=GPXTI15
PA2.Signal=S_TIM2_CH3
PA3.Signal=S_TIM2_CH4
PA4.GPIO_Label=SD_CS
PA4.Signal=GPIO_Output
PA5.Signal=SPI1_SCK
PA6.Signal=SPI1_MISO
PA7.Signal=SPI1_MOSI
PA8.Signal=S_TIM1_CH1
PA9.Signal=S_TIM1_CH2
PB0.Signal=S_TIM3_CH3
PB1.Signal=S_TIM3_CH4
PB10.Signal=USART3_TX
PB11.Signal=USART3_RX
PB12.GPIO_Label=OPEN
PB12.Signal=GPIO_Output
PB14.GPIO_Label=LOOP_O
PB14.Signal=GPIO_Input
PB15.GPIO_Label=LOOP_I
PB15.Signal=GPIO_Input
PB3.GPIO_Label=BTN_DATA
PB3.Signal=GPIO_Input
PB4.GPIO_Label=BTN_SW
PB4.Signal=GPXTI4
PB5.GPIO_Label=BTN_PLUS
PB5.Signal=GPIO_Output
PB6.Signal=USART1_TX
PB7.Signal=USART1_RX
PB8.Signal=I2C1_SCL
PB9.Signal=I2C1_SDA
PC13-TAMPER-RTC.Signal=GPIO_Output
PC14-OSC32_IN.Signal=RCC_OSC32_IN
PC15-OSC32_OUT.Signal=RCC_OSC32_OUT
PD0-OSC_IN.Signal=RCC_OSC_IN
PD1-OSC_OUT.Signal=RCC_OSC_OUT

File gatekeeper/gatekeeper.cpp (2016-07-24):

#include <avr/wdt.h>
#include <Arduino.h>
#include <ds3231.h>
#include <SdFat.h>
#include <MemoryFree.h>
#include "config.h"
#include "globals.h"
#include "toolbox.h"
#include "dthelpers.h"
#include <commsyms.h>
#include "serialout.h"
#include "serialbuf.h"
#include "decode433.h"
#include "gatehandler.h"
#include "intdb.h"
#include "sdfatlogwriter.h"

//////////////////////////////////////////////////////////////////////////////
void setuprelaypins( const uint8_t *pins, uint8_t size );
void processinput();
int getlinefromfile( SdFile &f, char* buffer, uint8_t buflen );
void updatedow( ts &t );
uint16_t importdb(uint16_t start, uint16_t end);

//////////////////////////////////////////////////////////////////////////////
void setup()
{
	Serial.begin( BAUD );
#ifdef VERBOSE
	delay(10);
	Serial.print( CMNT );
	for( char c = 0; c < 79; ++c ) Serial.print('-');
	Serial.println();
#endif

	memset( &g_time, 0, sizeof( g_time ));

	I2c.begin();
	I2c.timeOut(1000);

	g_display.init();		//	calls Wire.begin()

	g_display.print( freeMemory() );

	g_sdpresent = g_sd.begin( SS );
	g_display.print( ' ' );
	g_display.print( g_sdpresent );

#ifdef USE_FLASHDB
	bool dbinitsucc = g_db.init();
#else
	bool dbinitsucc = g_sdpresent && g_db.init();
#endif

	g_display.print( ' ' );
	g_display.print( dbinitsucc );

	g_indloop.init( PIN_INNERLOOP, PIN_OUTERLOOP, LOW );

	setup433();

	g_clk.init( DS3231_INTCN );
	g_lastdtupdate = millis();
	g_timevalid = g_clk.get( &g_time ) == 0;
	updatedow( g_time );

	bool loginitsucc = g_sdpresent && g_logger.init();
	g_display.print( ' ' );
	g_display.print( loginitsucc );

	g_outputs.set(0xf8);
	delay(500);
#ifdef REORDERED_IOEXT_PINS
	g_outputs.set(0x37);
#else	//	STRAIGHT_IOEXT_PINS
	g_outputs.set(0xc7);
#endif	//	STRAIGHT_IOEXT_PINS
	delay(500);
	g_outputs.set(0xff);

	g_display.clear();
	if(g_sdpresent)
	{
		SdFile	f;
		if(f.open("IMP"))
		{
			f.close();
			g_display.print("IMP");
			uint16_t	imported(importdb(0, 1023));
			if(imported != (uint16_t) -1) {
				g_display.print(' ');
				g_display.print(imported);
				g_sd.remove("IMP");
			} else
				g_display.print(F("FAIL"));

			delay(2000);
			g_display.clear();
		}
		if(f.open("CLR"))
		{
			f.close();
			g_display.print("CLR");
			g_db.cleanstatuses();
			g_sd.remove("CLR");
			g_display.clear();
		}
	}

	g_logger.log( logwriter::WARNING, g_time, F("Restart"), -1 );
	g_display.clear();
	g_display.updatedt(g_time, 0xff, g_timevalid);
	g_display.updateloopstatus(false, false);
	g_display.updatelastreceivedid(9999);
	g_display.updatelastdecision('X', 9999);

	wdt_enable(WDTO_1S);

#ifdef VERBOSE
	Serial.begin( BAUD );
	delay(10);
	Serial.print( CMNT );
	for( char c = 0; c < 79; ++c ) Serial.print('<');
	Serial.println();
#endif
}

//////////////////////////////////////////////////////////////////////////////
void loop()
{
	static gatehandler	handler( g_db, g_lights, g_indloop, g_display, 500 );
	unsigned long		now( millis() );
	uint8_t				dtcmask(0);
	bool				timevalid;
	bool				tvchanged;

	CHECKPOINT;

	if( now - g_lastdtupdate > 980 )
	{
		ts	t;
		timevalid = g_clk.get( &t ) == 0;
		tvchanged = timevalid != g_timevalid;
		if(tvchanged){
			g_logger.log( timevalid ? logwriter::INFO : logwriter::ERROR, g_time, timevalid ? F("TV") : F("TIV"), -1 );
			g_timevalid = timevalid;
		}

		if( t.sec != g_time.sec )
			dtcmask |= 1;
		if( t.min != g_time.min )
			dtcmask |= 2;
		if( t.hour != g_time.hour )
			dtcmask |= 4;
		if( t.mday != g_time.mday )
			dtcmask |= 8;
		if( t.mon != g_time.mon )
			dtcmask |= 0x10;
		if( t.year != g_time.year )
			dtcmask |= 0x20;
		if( tvchanged )
			dtcmask |= 0x40;

		if( dtcmask & 0x38 ) {
				g_time = t;
				updatedow( g_time );
		} else if( dtcmask &7) {
			g_time.sec = t.sec;
			g_time.min = t.min;
			g_time.hour = t.hour;
		}
		if( dtcmask ) {
			g_lastdtupdate = now;
			g_display.updatedt( g_time, dtcmask, g_timevalid );
		}
	}

	if( getlinefromserial( g_iobuf, sizeof( g_iobuf ), g_inidx) )
		processinput();

	handler.loop( now );

	if( g_codedisplayed != g_lrcode ) {
		uint16_t	id( getid( g_lrcode ));
		g_display.updatelastreceivedid( getid( id ));
		g_logger.log( logwriter::DEBUG, g_time, F("NewCode"), id );
		g_codedisplayed = g_lrcode;
	}
}

////////////////////////////////////////////////////////////////////////////////
//ISR( TIMER0_COMPA_vect )
//{
//	if( ++g_lastcheckpoint > 5000 ) {
//		pinMode( PIN_RESET, OUTPUT );
//		digitalWrite( PIN_RESET, LOW );
//	}
//}
//
//////////////////////////////////////////////////////////////////////////////
void setuprelaypins( const uint8_t *pins, uint8_t size )
{
	while( size > 0 ) {
		pinMode( *pins, OUTPUT );
		digitalWrite( *pins++, RELAY_OFF );
		--size;
	}
}

//////////////////////////////////////////////////////////////////////////////
void printrespok() {
	Serial.println( F( RESPS "OK"));
}

//////////////////////////////////////////////////////////////////////////////
void printresperr() {
	Serial.println( F( ERRS "ERR"));
}

//////////////////////////////////////////////////////////////////////////////
const char PROGMEM CMD_GET[] = "get";	//	get db record
const char PROGMEM CMD_SET[] = "set";	//	set db record
const char PROGMEM CMD_EXP[] = "edb";	//	export database
const char PROGMEM CMD_IMP[] = "idb";	//	import database
const char PROGMEM CMD_DMP[] = "ddb";	//	dump database
const char PROGMEM CMD_GDT[] = "gdt";	//	get datetime
const char PROGMEM CMD_SDT[] = "sdt";	//	set datetime
const char PROGMEM CMD_CS[] = "cs";		//	clear statuses
const char PROGMEM CMD_DS[] = "ds";		//	dump shuffle
const char PROGMEM CMD_DL[] = "dl";		//	dump log
const char PROGMEM CMD_TL[] = "tl";		//	reuncate log
const char PROGMEM CMD_IL[] = "il";		//	infinite loop
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

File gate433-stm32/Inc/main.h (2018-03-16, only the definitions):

#define SD_CS_Pin GPIO_PIN_4
#define SD_CS_GPIO_Port GPIOA
#define OPEN_Pin GPIO_PIN_12
#define OPEN_GPIO_Port GPIOB
#define LOOP_O_Pin GPIO_PIN_14
#define LOOP_O_GPIO_Port GPIOB
#define LOOP_I_Pin GPIO_PIN_15
#define LOOP_I_GPIO_Port GPIOB
#define BTN_CLK_Pin GPIO_PIN_15
#define BTN_CLK_GPIO_Port GPIOA
#define BTN_CLK_EXTI_IRQn EXTI15_10_IRQn
#define BTN_DATA_Pin GPIO_PIN_3
#define BTN_DATA_GPIO_Port GPIOB
#define BTN_SW_Pin GPIO_PIN_4
#define BTN_SW_GPIO_Port GPIOB
#define BTN_SW_EXTI_IRQn EXTI4_IRQn
#define BTN_PLUS_Pin GPIO_PIN_5
#define BTN_PLUS_GPIO_Port GPIOB

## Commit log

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2015-09-29 Using timer0 compare a interrupt to afterglow LED
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2015-11-03 test fixed to debug brain demaged remote control fix
    [interface.cpp]
2015-11-15 arm gatehandler && extdb
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2015-12-10 common added to boardtest
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2015-12-18 boardtest will not print time on serial if LCD presents.
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2015-12-19 lamp seems to be rady for action (manual test from boardtest)
2016-01-03 boardtest compile fix && remove trafficlights testing
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2016-01-05 using PCF8574 instead of arduino I/O pins for relay output
2016-01-07 hybriddb debugged&fixed, uses index based file opening boardtest use if ... else if ... instead of switch() in command processor
    [database.h, hybriddb.cpp, interface.cpp]
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2016-01-13 boardtest displays relay status on LCD
2016-01-20 boardtest tests 433MHz receiver
2016-01-24 timing issue fixed in decode433
    [config.h, gatekeeper.cpp]
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2016-01-28 zupapawah && few commands shortened, F() -> PROGMEM
    [gatekeeper.cpp, interface.cpp]
2016-01-30 bugfix: reboot in case of missing SD card
    [gatekeeper.cpp]
2016-01-30 gate relay handled by outputpin class eliminate m_[hig|low]value from outputpin
2016-01-31 gatekeeper log filling on receive bugfix
    [gatekeeper.cpp]
2016-02-02 boardtest clan database (cdb) command
2016-02-02 gatekeeper import/export command bugfix
    [gatekeeper.cpp]
2016-02-02 boardtest print free memory to LCD at startup
2016-02-02 preparing relay output gpio abstraction
2016-02-13 Squashed 'libs/TimerOne/' content from commit 9790739
    git-subtree-dir: libs/TimerOne
    git-subtree-split: 979073973b09aa5d084224fe351e7b46ed358f6e
2016-02-13 gk_simple: Fixing traffic lights pins (inside<->outside)
    [config.h]
2016-02-13 common: renaming flashdb to i2cdb, adding eepromdb
2016-02-13 boardtest: reverse 433 decoding switched on
    [config.h]
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2016-02-13 Squashed 'libs/I2C/' content from commit 806595c
    git-subtree-dir: libs/I2C
    git-subtree-split: 806595cb8c494b4e3876dc317c82c357bff9651c
2016-02-13 libs/I2C: added write16 and read16 functions
2016-02-14 serialspy: moved serialspy/libs/Timer to libs/Timer; ino->cpp
2016-02-17 gk_simple using libs/I2C
    ds3231 using libs/I2C
2016-02-17 I2c timeOut added (100 ms)
2016-02-17 boardtest: stress testintg I2C; switch off reversed RF bit order gatekeeper: switch off reversed RF bit order
    [config.h]
2016-02-17 libs/I2C: write16 bugfix
2016-02-17 libs/I2C_EEPROM, common/i2cdb, gk_simple: I2C_EEPROM refactor to use new I2C library
2016-02-18 libs/PCF8574: Wire->I2c testbed: i2cioexttest
2016-02-18 libs/LiquidCrystal_I2C: Wire->I2C testbed: test LCD in i2cioexttest
2016-02-18 boardtest: using new I2C lib based devices
2016-02-21 boardtest: incoming code logging
2016-02-22 codereader use I2C instead of Wire
2016-03-04 gk_simple: fix transit light anomaly, inductiveloop debouncing
    [gk_simple.cpp]
2016-03-05 gatekeeper: + I2C lib; + gatehandler invalid state protection; codereader: Enable I2C lib loadtest: include path fix (+common)
2016-03-06 createdb: gitignore case issue fix
2016-03-13 handling raw relay output pins the same as PCF8574 outputs (to switch between them easily)
2016-03-13 gk_simple: Switching green to red when induction loop changes during passage, holding it until there's no car on either loops.
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2016-03-17 gk_simple: use IO extender for relay output, import DB on startup if there is a file named "IMPORT" in SD card root
2016-03-17 gk_simple: eepromdb -> i2cdb
2016-03-21 gatekeeper: - Import DB on startup if there is a file named "IMPORT" in SD card root - fix last received code display - code should be received twice to be considered as valid input - timeout for PAS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
    [config.h, database.cpp, database.h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]
2016-03-23 importdb fix and optimalization
    [gatekeeper.cpp, gk_simple.cpp]
2016-03-23 DS3231 refactor; I2C error handling; DST handling; OSF handling
2016-03-25 * DS3231 full static class + DST capability moved to DS3231_DST + class DS3231 function calls replaced to DS3231_DST calls * gk_simple EEPROM.h fix
    [codereader.cpp, gatekeeper.cpp, gk_simple.cpp]
2016-03-27 * Read when OSF error present; DS3231::get void -> error; + g_clk; - ts.error; * osf_error fix (inverted); * m_checklevel temporary public; + DS3231_DST::m_checklevel test in DS3231Test
    [gatekeeper.cpp]
2016-03-27 gatekeeper: datetime update over-optimization bug fix
    [gatekeeper.cpp]
2016-03-28 libs/DS3231: manual-optimizing get & set for size boardtest: use DS3231 class for date&time
2016-03-31 libs/PCF8574: - all functions return error code - not calling read during write (use internal status) all projects: - use g_time for time keeping (instead of g_t, g_dt, etc) gatekeeper, gk_simple: - 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
    [arduinooutputs.cpp, codereader.cpp, gatekeeper.cpp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]
2016-04-01 codereader: I2c initialization (for I2C LCD) gk_simple: updating time before logging inductive loop change
2016-04-02 Eclipse Arduino plugin V3 conversion
2016-04-02 libs/LiquidCrystal_I2C: write() bugfix (printed only the first character of strings due to a bogus return value)
2016-04-08 gatekeeper: - trafficlights is a global now (as loop, db, etc) - switching on and off lights at restart - time invalid status appears on the display
2016-04-14 libs/i2c_eeprom: I2C error handling
    [hybriddb.cpp]
2016-04-17 barereader: LED eye-candy common/decode433: counting overruns (up to 255)
2016-05-03 boardtest: compile fix
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2016-07-24 gatekeeper: enable watchdog timer (!!!uno bootloader required!!!) ddb && dl: data lines start with ">" instead of ":" log dump: additional parameter to truncate after dump
2018-01-11 bluepill (STM32F103C8T6) controller firmware project beginning
    [gate433-stm32 Debug.cfg]
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2018-01-13 git subrepo clone git@git.pcmuhely.hu:compi/stm32goodies.git
    subrepo:
    subdir: "stm32goodies"
    merged: "cfe0653"
    upstream:
    origin: "git@git.pcmuhely.hu:compi/stm32goodies.git"
    branch: "master"
    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
2018-01-16 bluepill: RFDecoder: moved interrupt enablement to a separate Init() to avoid singleton initialization problem (get rid of SafeSingletonInitializer<> usage).
    [gate433-stm32.ioc, mainloop.cpp]
2018-01-16 bluepill: added SPI SD BSP and demo code
2018-01-16 bluepill: hardware design starts (kicad)
    [bluepill.kicad_pcb, bluepill.sch]
2018-01-18 hardware/stm32: bluepill schematics && PCB progress
    [Outputs.sch, bluepill.kicad_pcb, bluepill.sch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]
2018-01-18 bluepill Schematics 0.99
    [Outputs.sch, bluepill.kicad_pcb, bluepill.sch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]
2018-01-19 bluepill PCB progress
    [Outputs.sch, bluepill.kicad_pcb, eeprom.sch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]
2018-01-19 bluepill: PCB 0.9
    [Outputs.sch, bluepill.kicad_pcb, eeprom.sch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]
2018-01-20 bluepill PCB: SD Card socket turned around
    [Outputs.sch, bluepill.kicad_pcb, mcu.sch]
2018-01-22 bluepill-hardware: Final touches before manufacturing
    [bluepill.kicad_pcb]
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2018-02-04 all: callback interfaces are passed as reference instead of pointer ds3231: Date/time to string i2clcd: Print padding i2ceeprom: buffer to first parameter for Read/Write i2cmaster: Introduced "Defaul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
2018-02-04 gate433-stm32: database and i2cdb ported from atmel version pwmoutputs and smartlights are working MainLoop class introduced
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2018-02-06 bluepill-hardware: few modifications on PCB after receiving the first proto panel
    [bluepill.kicad_pcb]
2018-02-08 i2cmaster: Passing references to interfaces instead of pointers
2018-02-08 i2ceeprom: NeedPoll() bugfix
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2018-02-08 i2cdb error handling
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2018-02-13 gate433-stm32: incoming codes are logged to SD SD log can be dumped to serial
2018-02-20 stm32 board test added
    [gate433-stm32-boardtest Debug.cfg]
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2018-02-24 gate433-stm32: Can be tested (config eeprom handling still needs to be implemented)
2018-03-03 DS3231: Temperature fixed point int instead of float
2018-03-03 gate433-stm32: UART: UART1 speed back to 115200, UART3 activated and handled the same as UART1 Timer initialization in main.c to shorten full power period for all lights on boot gt (Get Temperature) 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
    [database.h, gate433-stm32.ioc, main.c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]
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2018-03-08 bluepill commandprocessor: new logic to handle renge for CS, handlers commented (function) sdlogwriter: const correctness, log queue mainloop: log if usart::Receive fails, log queue support
    [mainloop.cpp]
2018-03-12 bluepill: gate opening bugfixes
    [mainloop.cpp]
2018-03-16 Bluepill: Change rotary encoder button line to EXTI Decrease interrupt priority of everything except I2C
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2018-03-17 i2clcd: removed inline from private finctions, added one char Print
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2018-03-25 bluepill: transit timeout fix
    [mainloop.cpp]
2018-04-16 Added FreeCAD model of the case for STM32 version
    [GateKeeperCase.fcstd]
2018-05-01 bluepill: slightly modified housing
    [GateKeeperCase.fcstd]
2018-05-01 bluepill: exti handler hardfault fix
    [mainloop.cpp]

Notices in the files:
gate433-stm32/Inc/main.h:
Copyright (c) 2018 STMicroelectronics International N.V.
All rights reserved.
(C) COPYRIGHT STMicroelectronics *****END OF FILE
